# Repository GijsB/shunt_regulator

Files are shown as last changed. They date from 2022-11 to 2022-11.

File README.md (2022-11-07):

# Low cost shunt regulator
This repository contains the design of a shunt regulator that's designed to be easy to manufacture and mount onto the front of my power supply. This readme will briefly describe the design and it's properties.

## Rationale
Most low-cost (lab/bench) power supplies are only able to supply power, they are not able to sink it. This becomes a problem when powering motor controllers, where the energy generated by "braking" cannot be dissipated elsewhere. I'd like to connect a motor controller to my power supply, as far as I know, there wasn't a cheap/simple solution that would allow me to do that safely. So I decided to try to develop my own solution.

## Requirements
 - Mount right on the binding-posts of my power supply
 - Inherently safe, no chance of burning my house down!
   - Maximum component temperature of <100 degC.
   - Fuses to limit further overloading.
 - Voltage range: 24V - 55V
 - Peak current dissipation: >5A
 - Continuous power dissipation: >5W, for example: 
   - Brake a 1000 gcm^2 rotor, from 3.000 RPM to 0 RPM every second.
   - Brake a 33 gcm^2 rotor from 16.000 RPM to 0 RPM every second.
 - Maximum (one time) energy pulse: 25 Joule
   - Enough to brake a 5000 gcm^2 rotor from 3.000 RPM to 0 RPM.
 - I'd like to use as many "jellybean" components as possible, to keep the cost down and to enable cheap manufacturing services.

## Design
The global design can be summarized by a comperator, a MOSFET, a polyfuse and some resistors. The picture below illustrates the circuit.

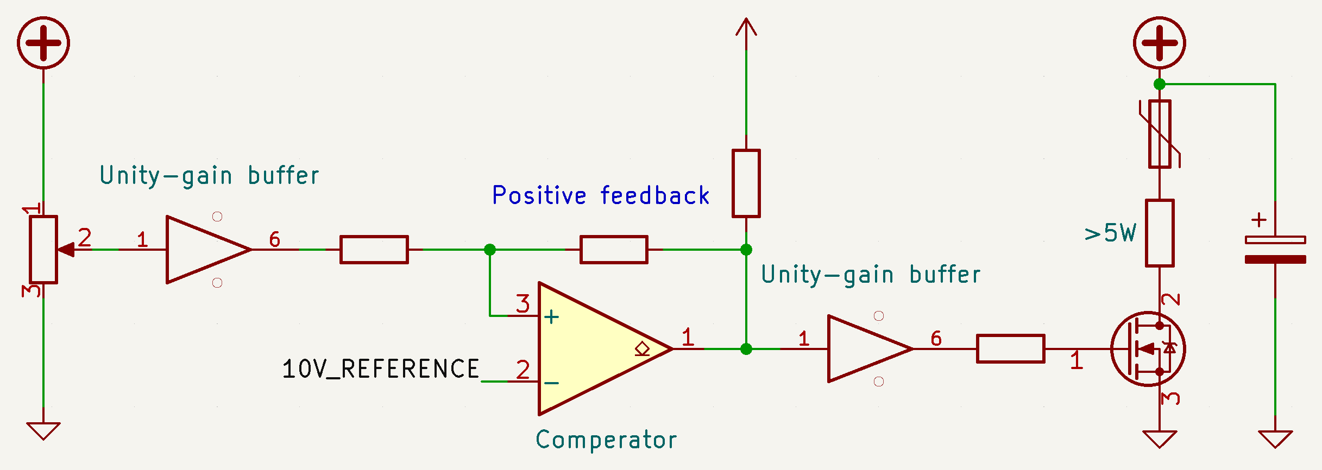
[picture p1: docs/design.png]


The idea is that the comperator simply enables the MOSFET when the bus voltage is higher than a set limit. There is some positive feedback for a bit of hysteresis: To prevent fast fluttering of the MOSFET. The voltage bus has significant capacitance, so the voltage doesn't instantly drop to 0, it "depletes" the capacitors until the voltage level is acceptable again.

The picture below shows the PCB design, it's shaped to fit around my power supply (Owon SPE-series).

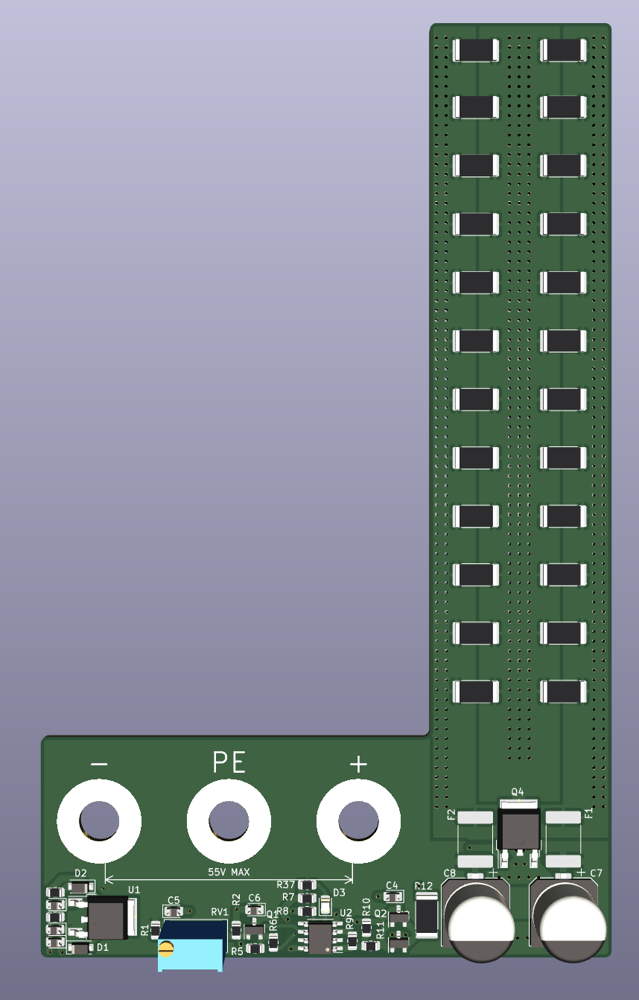
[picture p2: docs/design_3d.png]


## Simulation
An LTSpice simulation is made to validate the design before prototyping. A constant-current source simulates the regenerative braking of a motor. 

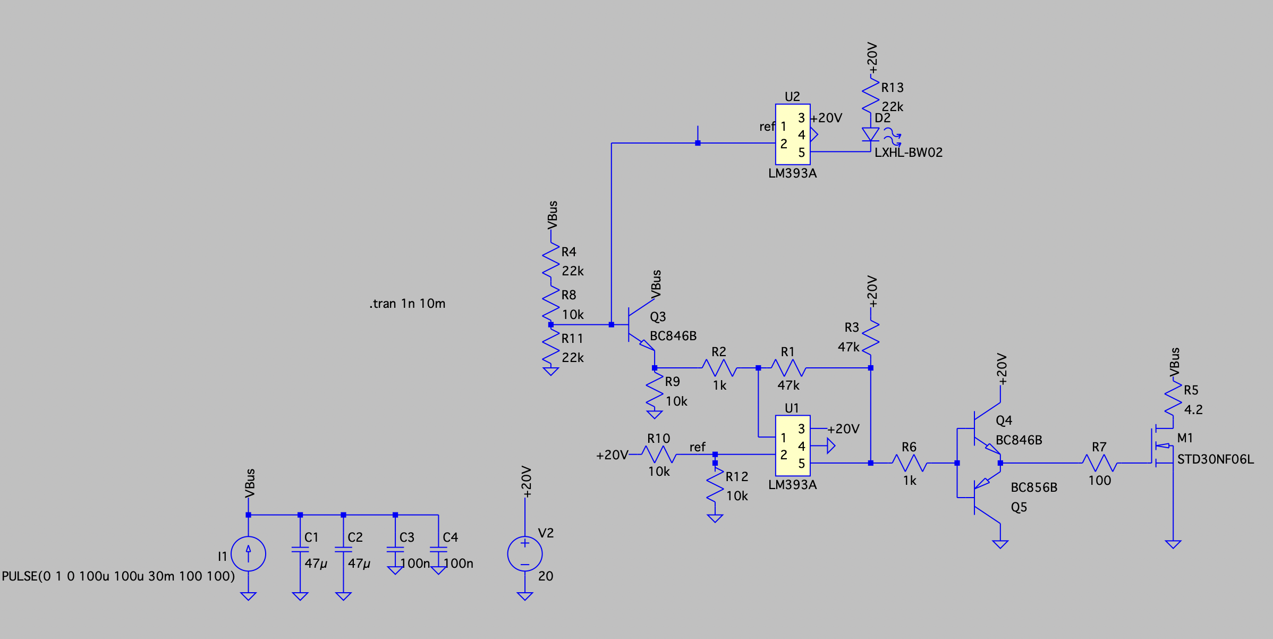
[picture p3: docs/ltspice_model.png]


The behaviour is as expected, the voltage is constrained, it looks like a saw-tooth or triangular wave depending on the brake current. The image below shows the bus voltage in green and the current through the resistors in blue.

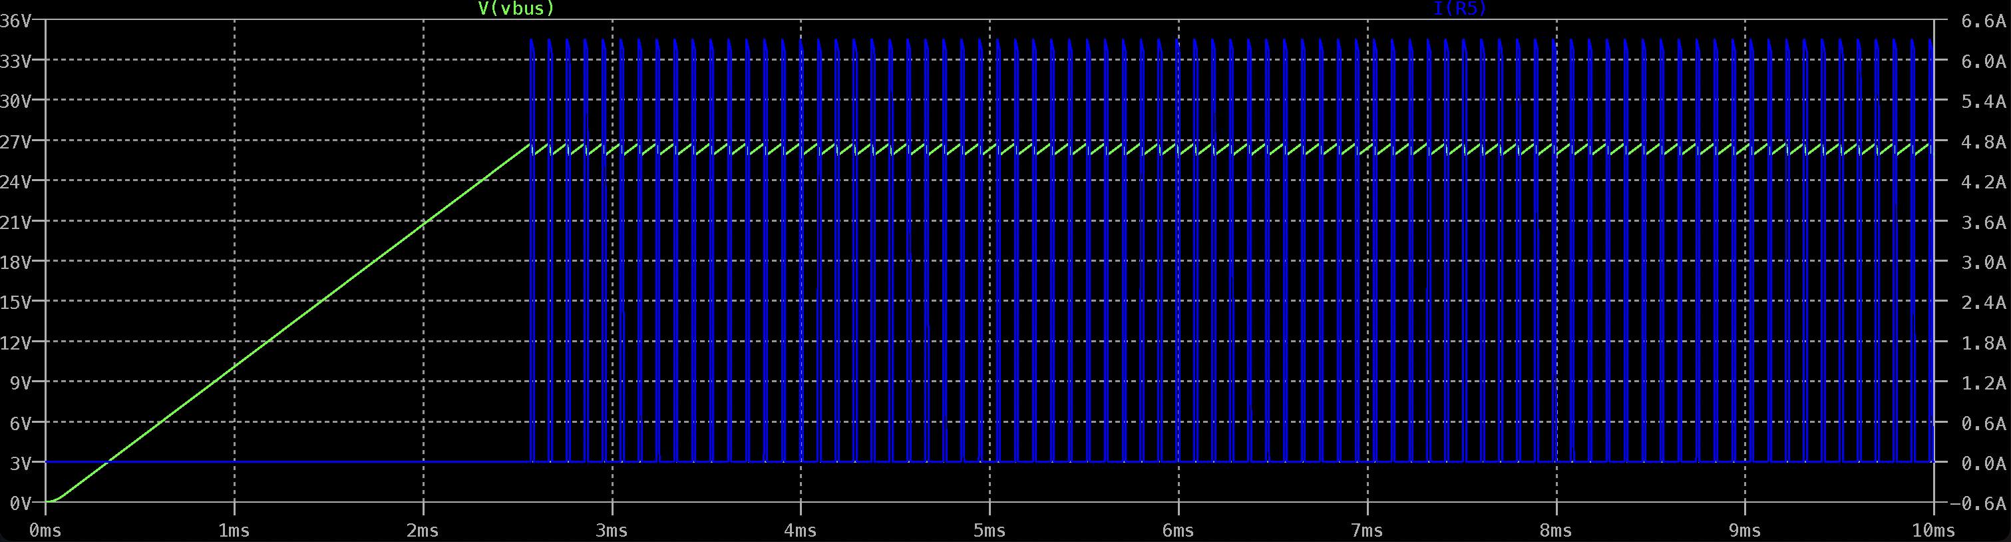
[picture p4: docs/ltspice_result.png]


The image below shows a zoomed-in view.

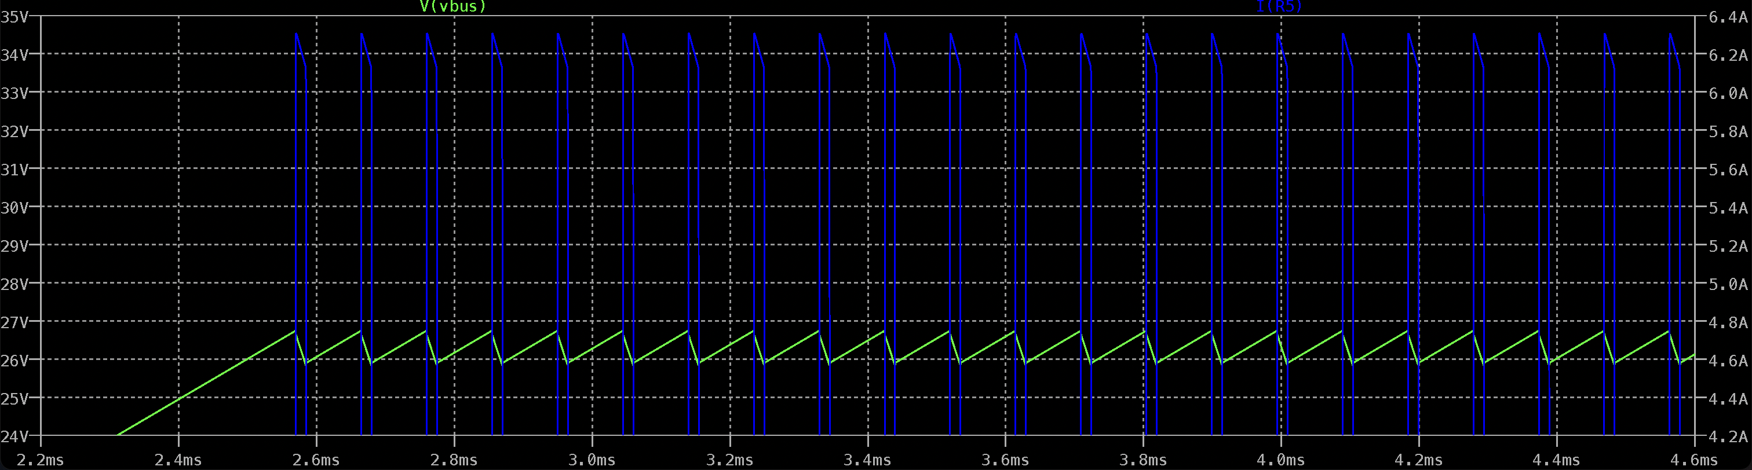
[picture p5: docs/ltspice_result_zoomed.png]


## Usage
 1. Identify the maximum safe voltage, this is the voltage that shall not be exceeded: Vmax.
 2. Set the voltage of the power supply <B>3 volts below Vmax</B>.
 3. Set the current limit of the power supply to 50mA.
 4. Enable the power supply.
 5. Turn the potentiometer until the LED is off, but it's right below turning on.
 6. Increase the power supply voltage, make sure the LED turns on. Keep slowly increasing the voltage, verify that the current increases rapidly before Vmax is reached.
 7. Disable the power supply voltage to 3 volts below Vmax again. Lower is even better, if your application allows.
 8. Increase the power supply current limit again to whatever your application requires.

## Experiments
WARNING: This device is not fully verified yet

### Power supply test
In this test, the shunt regulator is connected to a power supply. The power supply has a current limit of 500mA, the shunt regulator should limit the voltage. The picture below shows the resulting waveform. The yellow trace represents the power supply voltage, the blue trace represents the current from the power supply to the shunt regulator.

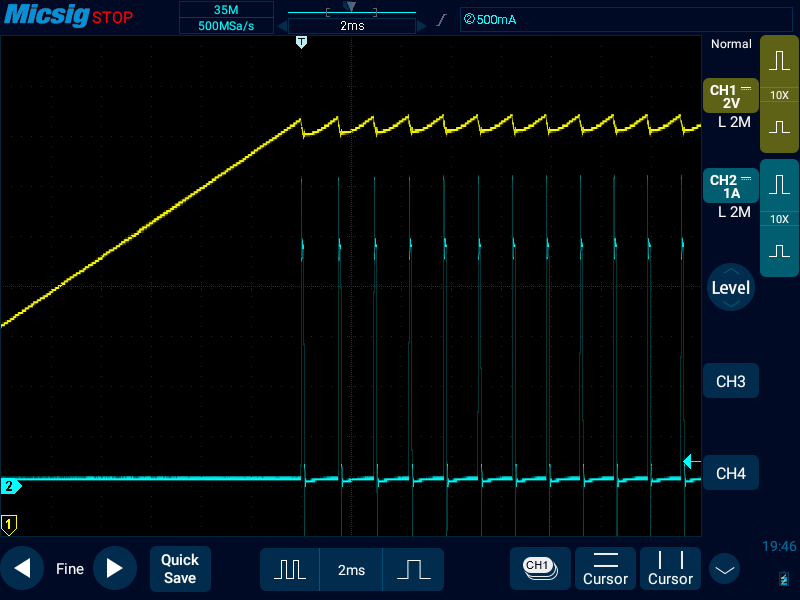
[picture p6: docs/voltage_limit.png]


### Braking a motor from 1200 RPM to 0 RPM
The main purpose of this shunt regulator is to be able to connect motor-controllers to this power supply, so this test verifies that it will effectively limit the voltage when and ESC is (regeneratively) braking a motor.

The yellow trace represents the system voltage, the blue trace represents the current between the ESC and the PSU + Shunt regulator.

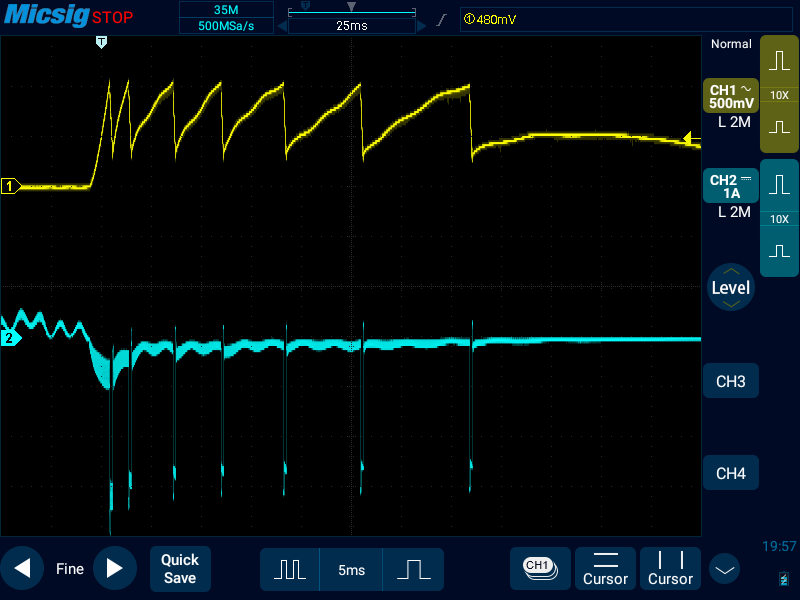
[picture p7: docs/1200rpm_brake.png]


The screenshot below shows the same waveform, but zoomed in.

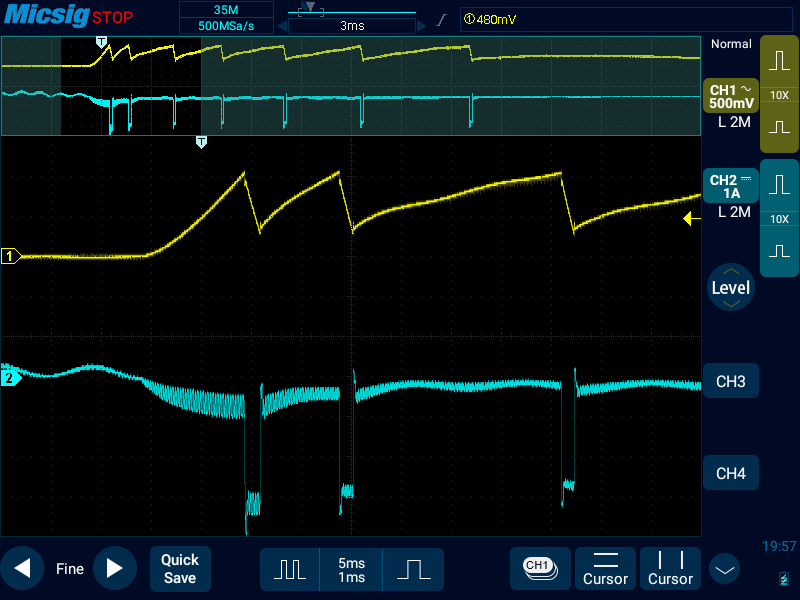
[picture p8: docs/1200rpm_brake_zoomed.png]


### Braking a motor from 2500 RPM to 0 RPM
This test is identical to the previous one, but with 4 times the amount of energy.

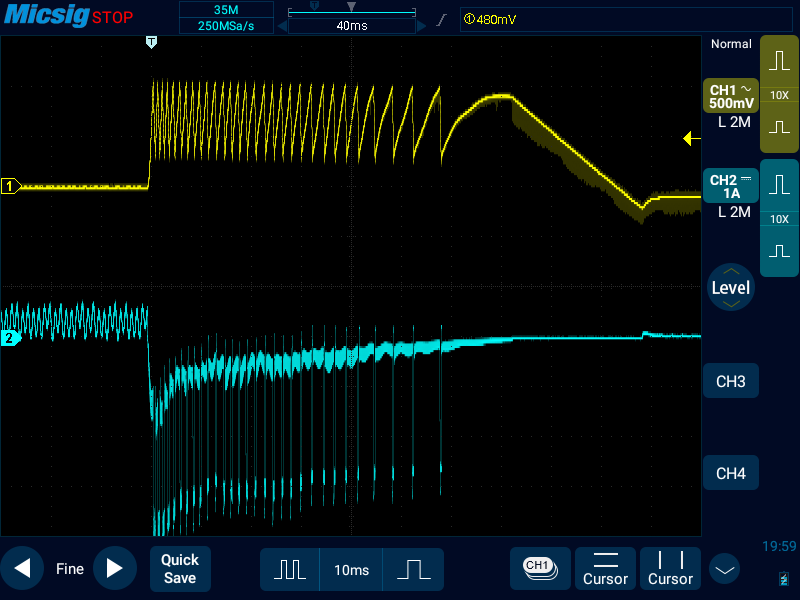
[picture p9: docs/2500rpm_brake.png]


The screenshot below shows the same waveform, but zoomed in.

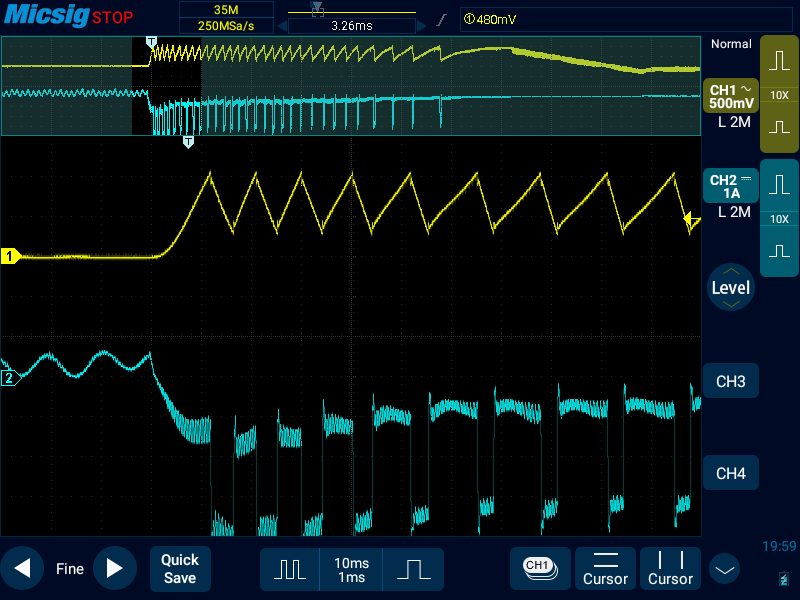
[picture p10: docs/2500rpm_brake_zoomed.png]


### Conclusion
It looks like the shunt regulator works, the bus voltage is effectively limited.

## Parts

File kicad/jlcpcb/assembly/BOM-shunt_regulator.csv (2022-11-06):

Comment | Designator | Footprint | LCSC
1k | R11,R6 | R_0805_2012Metric | C17513
22k | R1,R2,R37 | R_0805_2012Metric | C17560
240 | R3 | R_0805_2012Metric | C17572
47k | R10,R9 | R_0805_2012Metric | C17713
10k | R5,R7,R8 | R_0805_2012Metric | C17724
47u | C7,C8 | CP_Elec_10x10 | C178377
3k6 | R4 | R_0805_2012Metric | C18359
500 mA | F1,F2 | Fuse_2920_7451Metric | C269176
100n | C1,C5,C6 | D_0805_2012Metric | C28233
1u | C2,C3,C4 | D_0805_2012Metric | C28323
100 | R12,R13,R14,R15,R16,R17,R18,R19,R20,R21,R22,R23,R24,R25,R26,R27,R28,R29,R30,R31,R32,R33,R34,R35,R36 | R_2512_6332Metric | C31885
30N06 | Q4 | TO-252-2 | C369599
BC856B | Q3 | SOT-23 | C424398
100k | RV1 | Potentiometer_Bourns_3296W_Vertical | C48084
SM4007PL | D1,D2 | D_SOD-123F | C64898
LM317_TO-252 | U1 | TO-252-2 | C75510
LM393 | U2 | SOIC-8_3.9x4.9mm_P1.27mm | C7955
LED | D3 | LED_0805_2012Metric | C84256
BC846B | Q1,Q2 | SOT-23 | C87062
Screw_Terminal_01x03 | J1 | Owon SPE terminals

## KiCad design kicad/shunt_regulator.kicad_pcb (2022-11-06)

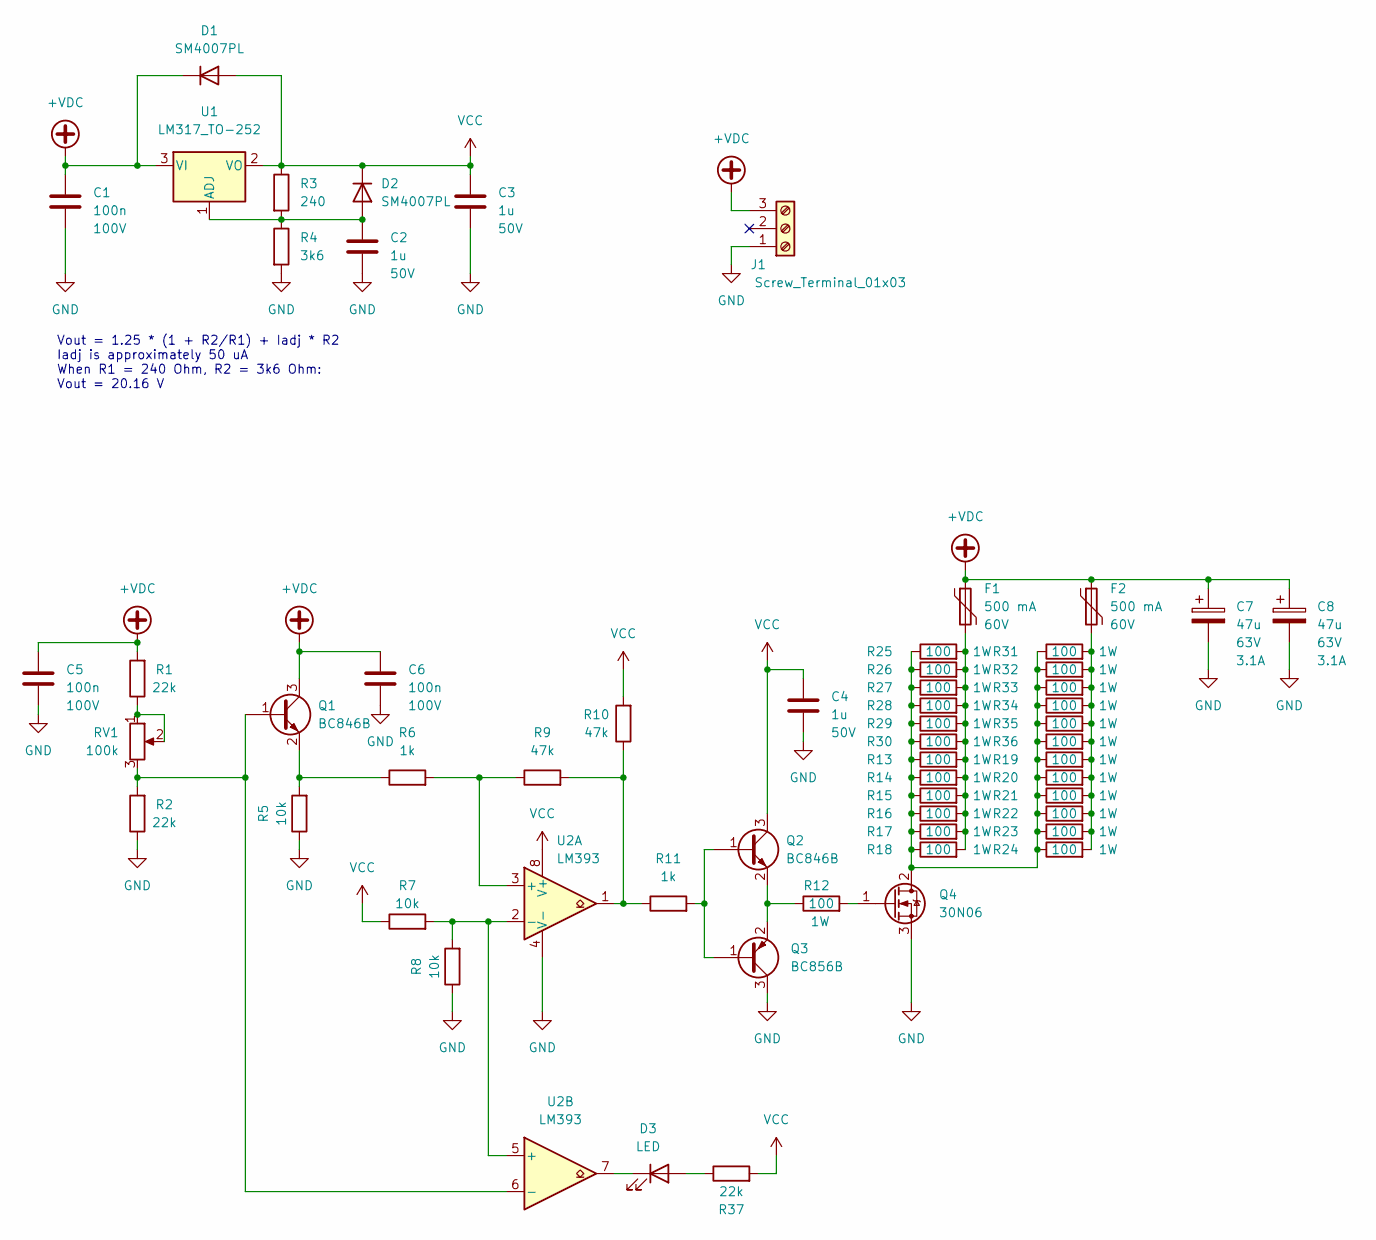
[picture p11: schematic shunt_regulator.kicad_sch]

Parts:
C1, C5, C6: 100n; D_0805_2012Metric; Voltage 100V; LCSC C28233
C2, C3, C4: 1u; D_0805_2012Metric; Voltage 50V; LCSC C28323
C7, C8: 47u; CP_Elec_10x10; Voltage 63V; LCSC C178377
D1, D2: SM4007PL; D_SOD-123F; LCSC C64898
D3: LED; LED_0805_2012Metric; LCSC C84256
F1, F2: 500 mA; Fuse_2920_7451Metric; Voltage 60V; LCSC C269176
J1: Screw_Terminal_01x03; Owon SPE terminals
Q1, Q2: BC846B; SOT-23; LCSC C87062
Q3: BC856B; SOT-23; LCSC C424398
Q4: 30N06; TO-252-2; LCSC C369599
R1, R2, R37: 22k; R_0805_2012Metric; LCSC C17560
R3: 240; R_0805_2012Metric; LCSC C17572
R4: 3k6; R_0805_2012Metric; LCSC C18359
R5, R7, R8: 10k; R_0805_2012Metric; LCSC C17414
R6, R11: 1k; R_0805_2012Metric; LCSC C17513
R9, R10: 47k; R_0805_2012Metric; LCSC C17713
R12, R13, R14, R15, R16, R17, R18, R19, R20, R21, R22, R23, R24, R25, R26, R27, R28, R29, R30, R31, R32, R33, R34, R35, R36: 100; R_2512_6332Metric; LCSC C31885
RV1: 100k; Potentiometer_Bourns_3296W_Vertical; LCSC C48084
U1: LM317_TO-252; TO-252-2; LCSC C75510
U2: LM393; SOIC-8_3.9x4.9mm_P1.27mm; LCSC C7955

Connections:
+VDC: C1.1, C5.1, C6.1, C7.1, C8.1, D1.1 (K), F1.1, F2.1, J1.3, Q1.3 (C), R1.2, U1.3 (VI)
GND: C1.2, C2.2, C3.2, C4.2, C5.2, C6.2, C7.2, C8.2, J1.1, Q3.3 (C), Q4.3 (S), R2.1, R4.2, R5.1, R8.1, U2.4 (V-)
unnamed: C2.1, D2.2 (A), R3.2, R4.1, U1.1 (ADJ)
unnamed: D3.1 (K), U2.7
unnamed: D3.2 (A), R37.1
unnamed: F1.2, R13.2, R14.2, R15.2, R16.2, R17.2, R18.2, R25.2, R26.2, R27.2, R28.2, R29.2, R30.2
unnamed: F2.2, R19.2, R20.2, R21.2, R22.2, R23.2, R24.2, R31.2, R32.2, R33.2, R34.2, R35.2, R36.2
unnamed: Q1.1 (B), R2.2, RV1.3, U2.6 (-)
unnamed: Q1.2 (E), R5.2, R6.1
unnamed: Q2.1 (B), Q3.1 (B), R11.2
unnamed: Q2.2 (E), Q3.2 (E), R12.1
unnamed: Q4.1 (G), R12.2
unnamed: Q4.2 (D), R13.1, R14.1, R15.1, R16.1, R17.1, R18.1, R19.1, R20.1, R21.1, R22.1, R23.1, R24.1, R25.1, R26.1, R27.1, R28.1, R29.1, R30.1, R31.1, R32.1, R33.1, R34.1, R35.1, R36.1
unnamed: R1.1, RV1.1, RV1.2
unnamed: R6.2, R9.1, U2.3 (+)
unnamed: R7.2, R8.2, U2.2 (-), U2.5 (+)
unnamed: R9.2, R10.1, R11.1, U2.1
VCC: C3.1, C4.1, D1.2 (A), D2.1 (K), Q2.3 (C), R3.1, R7.1, R10.2, R37.2, U1.2 (VO), U2.8 (V+)

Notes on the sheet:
Vout = 1.25 * (1 + R2/R1) + Iadj * R2 Iadj is approximately 50 uA When R1 = 240 Ohm, R2 = 3k6 Ohm: Vout = 20.16 V

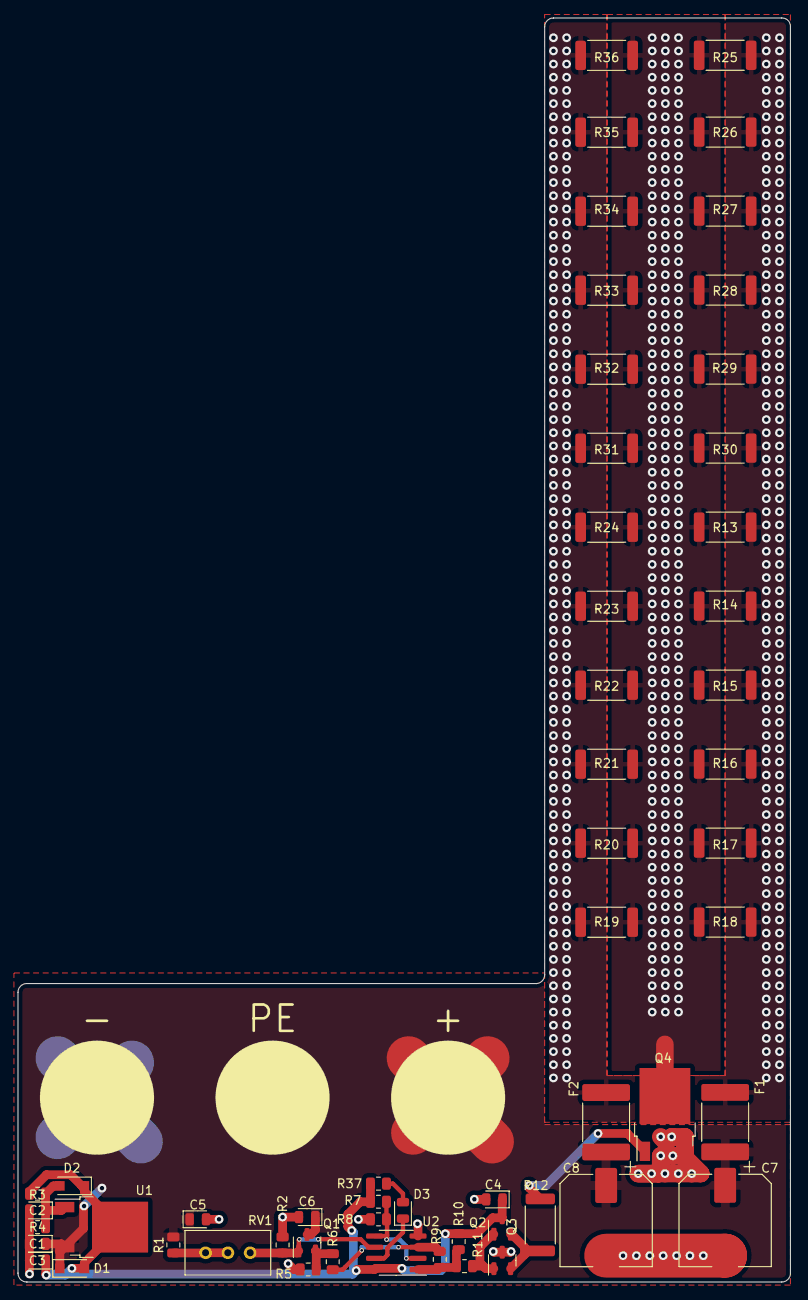
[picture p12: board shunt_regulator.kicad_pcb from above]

Board: 2 copper layers, 88.0 x 144.0 mm, 58 parts (0 on the bottom side), 18 nets.

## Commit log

2022-10-16 First kicad schematic and model
    [shunt_regulator.kicad_pcb, shunt_regulator.kicad_sch]
2022-10-22 Finished design
    [shunt_regulator.kicad_pcb, shunt_regulator.kicad_sch]
2022-10-24 Changed the power resistor footprint from 1210 to 2512
    [BOM-shunt_regulator.csv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]
2022-11-02 Fixed the footprint of the power supply, the pins where too close together
2022-11-02 Fixed footprint
    [shunt_regulator.kicad_pcb]
2022-11-02 Fixed a push-pull transistor that was the wrong way around
    [shunt_regulator.kicad_pcb, shunt_regulator.kicad_sch]
2022-11-02 Flipped input of LED comperator
    [shunt_regulator.kicad_pcb, shunt_regulator.kicad_sch]
2022-11-03 Changed the LCSC number of the 10k resistors
    [shunt_regulator.kicad_sch]
2022-11-05 Created more space for dissipation resistors, this way less heat is dunped into the fuses (increasing their rating)
    [shunt_regulator.kicad_pcb]
2022-11-05 Restructured repo such that the spice model would have it's own folder
    [BOM-shunt_regulator.csv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]
2022-11-05 Written the README up until the experiments
    [shunt_regulator.kicad_pcb]
2022-11-06 Updated production outputs and added the one time pulse energy to the README requirements
    [BOM-shunt_regulator.csv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]
